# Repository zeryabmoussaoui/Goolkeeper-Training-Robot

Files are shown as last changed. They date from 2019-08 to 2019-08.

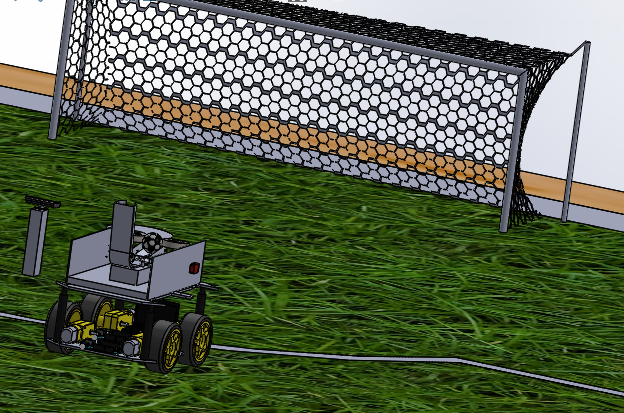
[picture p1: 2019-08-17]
hardware/mechanics/images/cad/Back_view.PNG

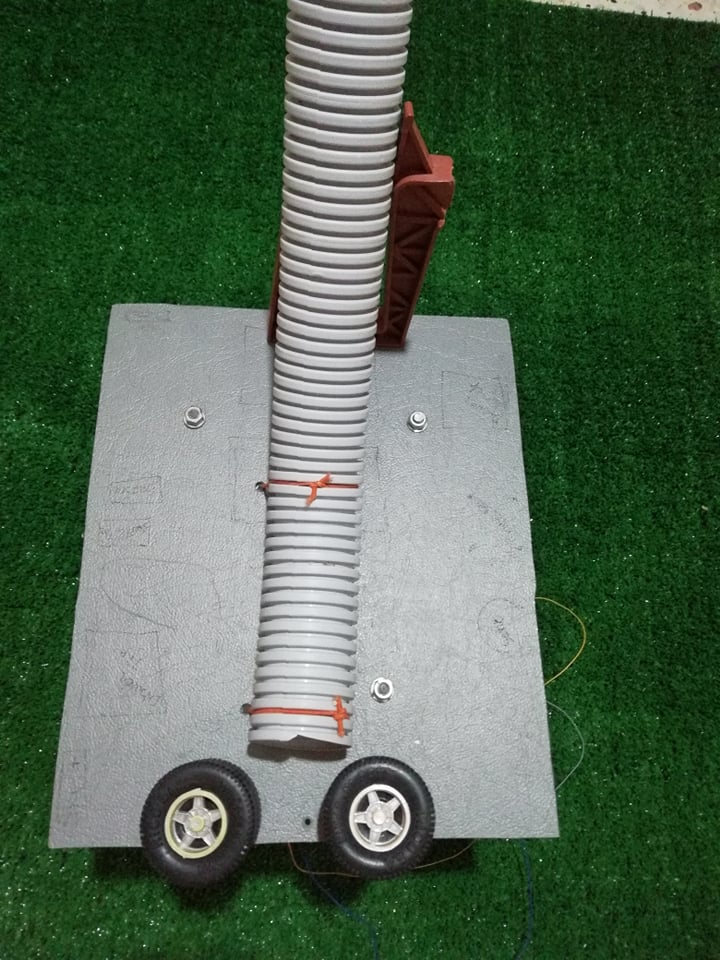
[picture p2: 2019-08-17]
hardware/mechanics/images/prototype/storage system/1.jpg

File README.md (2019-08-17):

# Goolkeeper-Training-Robot
In order to obtain the Engineering diploma in Automation field at the National Polytechnic School (Algeria) and in collaboration with the Central school of Electronics (France), I present to you my final thesis project, entitled **“Goalkeeper Training Robot”**.



## Summary
The project consists on the modeling and the realization of an autonomous robot that shoots
and evaluates the performances of a soccer goalkeeper based on his reactions.
Using a camera and a 3D human pose estimator, the system can detect and modelize the
goalkeeper’s physical gestures.
Finally, it proposes using artificial intelligence the suitable decision for the future exercises,
which maximizes the player’s performances.

## Folder structure
+ **README** 
  
+ **software/**
     - README
          - § Tool (Requirements , etc)
          - § Architecture (State-machine)
     - launch-train-goalkeeper.py 
     - launch-simulation.sh  
     - utils/ 
          - compute_pose.py
          - analyze_pose.py
          - send_navigation_mav.py
          - etc
+ **hardware/**
     - README
          - § List of components (existent and missing ones) 
     - mechanics/ 
          - cad_files/
          - images/
     - electronics/
          - cad-files/
          - images/
+ **articles/**
     - english
          - summary.docx 
          - summary.pdf
     - french
          - Mémoire_STIHI_Maha_ENP.pdf

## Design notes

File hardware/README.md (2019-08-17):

# Goolkeeper-Training-Robot

# Hardware

## List of available components 
| Component | Technical reference |
| --- | --- |
| DC motors | Pololu 12VDC, 350rpm 100:1 Gearmotor w/64 CPR Encoder | 
| DC motors | DC 12v motor | 
| Motor driver  | Cytron 10A 5-30V Dual Channel DC Motor Driver | 
| Autopilot | Pixhawk PX4 2.4.8 |
| Power supply  | DC 5v and 12v |
| Lipo battery  | Lipo 11.1 v 2200mah battery |
| Controling card  | Raspberry Pi 3 B+ |

## List of missing components 

| Component | Technical reference |
| --- | --- |
| Stepper motor | 2.8 V 1.68A 4.4kg-cm RepRap SOYO |
|  Motor driver | Single stepper motor driver 10-30V 4A |
| Power cable | Power cable for the Pixhawk PX4 2.4.8  | 

## Prototype 
Using the stated components and the mechanical structure design, we build the prototype of the system to represent most of the functionalities of the real system.

The steps of the construction are as follow :

**1. The base of the robot :**



**2. Shooting system :** 



**3. Storage system :** 



**4. Assembled robot :**



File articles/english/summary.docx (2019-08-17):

Design and Realization of a Mobile Robot to train Football Goalkeepers

Realized by: Maha Stihi

Abstract
The project consists on the modeling and the realization of an autonomous robot that shoots
and evaluates the performances of a soccer goalkeeper based on his reactions.
Using a camera and a 3D human pose estimator, the system can detect and modelize the
goalkeeper’s physical gestures.
Finally, it proposes using artificial intelligence the suitable decision for the future exercises,
which maximizes the player’s performances.
Key words: Soccer goalkeeper, Training, Robot, 3D human pose estimation, Artificial
intelligence.

I. Introduction

Robotics has many areas of application. Originally, the robots been established in industries (as early as 1961) to perform repetitive tasks with a constant precision. Now, after the development of technology and especially after the introduction of artificial intelligence, we find robots implanted in almost all fields and used for all purposes, even in an environment close to humans. The artificial intelligence algorithms and robots are known to be introduced to automate tasks and replace human work. For example, "LawGeex" uses the latest technologies in intelligence, machine learning, analysis text and natural language processing to review and understand documents legal [1]. This smart system can replace hundreds of legal advisers who are often overworked to review daily contracts, which was very expensive in time, money and human resources. In robotics and more specifically in sports field, athletes are also among the recipients of technological assistance. We can cite:

- Mobile robots developed by the "Japanese Volleyball Association" with the help of researchers from Tsukuba University to help the team's attackers National Women's Training [2] (Figure 1.a);

- The tennis ball shooter robot that gives precise and intensive training to players [3] (Figure 1.b);

- And also the mobile robot "MVP" that simulates the veneer of football players American [4] (Figure 1.c).

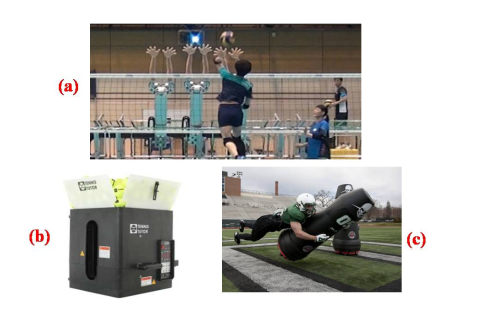
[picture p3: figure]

Figure 1 - Examples of sports robots

II. Problematic

In the field of sport, some techniques need a lot of training to master them. Even in the best teams in the world, the number of coaches is very limited, especially in football, for 4 goalkeepers only one coach is available. Therefore, players from different positions will help each other to ensure their training. What makes some players spend part of their workouts helping goalkeepers practicing.

Decision making has always been a difficult task; choose which player to introduce in a match is made by coaches based on several criteria like the physical and tactical performances of the player in the training. This decision is related to the skills and experiences of coaches, so it can be biased.

Injuries are the biggest enemies of athletes. Once the injury is treated medially, the player goes through special programs to return to his former performance. The follow-up of the players after a stoppage of play is a very important part; given that it determines the time it takes to get back to competition, so it can affect the whole team if he is an important player. The choices of the type and intensity of exercises are usually set by both medical and technical parties. By consequence, having a compromise between the medical team that wants to ensure that the player can play in security and the technical team that wants the player to return to the pitch as soon as possible is very difficult to ensure, so a neutral third opinion is highly recommended.

With this project, we want to contribute to a part of the sport field, which is the training of football goalkeepers to minimize the problems illustrated above.

We propose a mobile robot, to help the goalkeeper’s coach during the trainings and also to test the players’ performances with the help of the analysis of the goalkeeper's gestures based on well-studied exercises. Subsequently, the robot provides detailed technical reports to help the coach take the right decisions. It will also have an artificial intelligence that will help to propose the future exercises to work on to keep track of injuries and maximize players’ performances.

III. Specifications

In order to achieve our strategy, the robot must be able to:

- Move on a flat surface to position the coordinates (x, y) on the pitch;

- Turn it in a flexible way to orient the part of the shot at an angle θ with a good precision;

- Locate on the ground using odometers;

- Store the balls in the robot using the available height;

- Shoot the balls with a speed and a predefined trajectory;

- Estimate the pose of the goalkeeper;

- Analyze and study the goalkeeper's reaction to the shot.

IV. System Architecture

The modeling of the system allows us to establish a work plan of the project, by identifying the essential parts of the project and the relationships between them. This modeling allows us to have the architecture overall system.

The architecture of mobile robots consists of four essential parts:

• Mechanical structure and motorization;

• Location system;

• Security organs;

• Information processing system and task management.

This architecture is usually presented as a block diagram, each block represents a feature of the system, and the blocks are then linked together based on the logic of system operation.

Our project is more complex than a simple mobile robot because we have a ball shooting functionality as well as another external data processing feature of the goalkeeper. So, more blocks are presented in the architecture of our system.

Security organs are not taken into account in our work. Only basic security components are set up in our system.

To represent the system parts and its logic process, we use the Moore state diagram as followed:

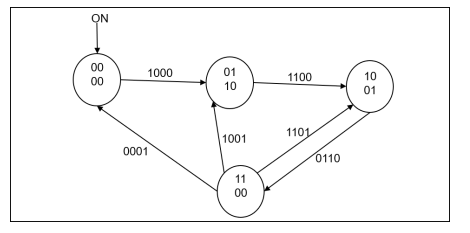
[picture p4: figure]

Outputs:

Motors moving & motors shooting

Position arrived

Shoot

Analysis

done

Exercise

State :

00 : initialization

01 : Move

10 : Shoot

11 : Analysis

Transition :

x | x | x | X

Fig 2– Moore diagram (state diagram)

In order to program this state machine in the future, we prefer to represent the state machine as known for the programmers:

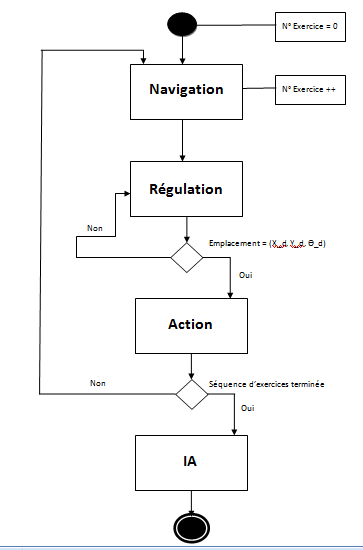
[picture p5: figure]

Fig 3 – State machine

V. Mechanical Conception

The mechanical design was done by SolidWorks, version 2016.

V.1. Mobile Robot Base

The top of the robot is dedicated to the shooting so, it’s bulky and heavy therefore, the upper surface must be spacious and solid. At the same time, robot must stay in balance to ensure a good trip on the pitch. So, we opted for a four-wheeled mobile base model "Rover" (Figure 4).

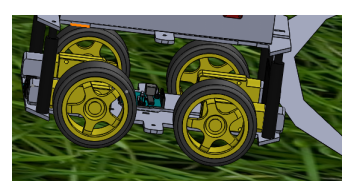
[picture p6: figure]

Figure 4 – Rover

V.2. Ball Shooting System

In order to ensure a variety of training exercises by our robot, it is necessary that the shooting system has the ability to generate different types of trajectories for the ball.

For this, this part of the robot must not be totally fixed. With two engines (Figure 5), a shooting angle of 30◦maximum can be achieved to aim at any point on the height of the goals.

On the other hand, the shooting is done using two motorized wheels with separate speeds, which makes it possible to vary the exit trajectory while varying the speeds of the two motors separately (Figure 5).

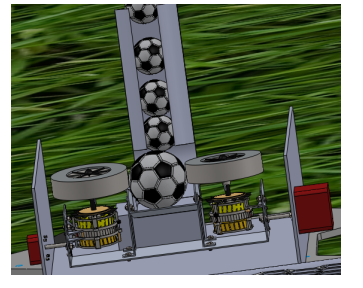
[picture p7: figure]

Figure 5 – Upper part of shooting balls

V.3. Storage System

To achieve several shots fast, automated, and also to avoid the human being assistance, a balloon storage system is necessary. We designed a cylindrical device with a diameter of 28 cm, which allows stacking footballs (diameter 22 cm) vertically.

Only one ball must pass at a time and on demand to the shooting part, for this a motorized controllable blocking system is implemented (Figure 6).

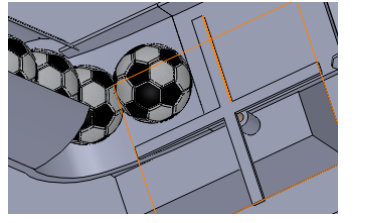
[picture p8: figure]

Figure 6 – Ball blocking system

V.4. Robot Assembly

The previous three parts are assembled to form our robot balls shooter (Figures 7 and 8).

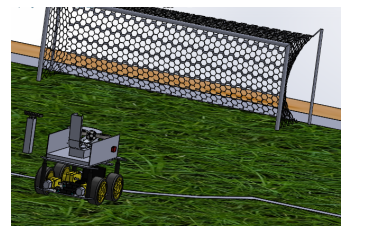
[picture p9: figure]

Figure 7 – Back view of the robot.

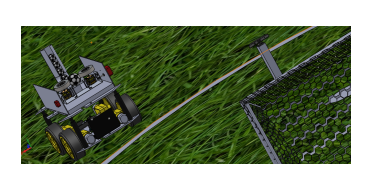
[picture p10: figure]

Figure 8 – Front view of the robot.

VI. Rover Simulation

Before jumping into the realization of the real robot and test the navigation system, it’s preferable to test the programs and functionalities with a simulation.

Ardupilot is an open source (https://en.wikipedia.org/wiki/Open-source_software), unmanned vehicle (https://en.wikipedia.org/wiki/Uncrewed_vehicle) Autopilot navigation software capable of controlling autonomously different types of vehicles:

- Multirotor (https://en.wikipedia.org/wiki/Multirotor) drones
- Fixed-wing and VTOL (https://en.wikipedia.org/wiki/VTOL) aircraft (https://en.wikipedia.org/wiki/Model_aircraft)
- Helicopters (https://en.wikipedia.org/wiki/Radio-controlled_helicopter)
- Ground rovers (https://en.wikipedia.org/wiki/Radio-controlled_car)
- Boats
- Submarines (https://en.wikipedia.org/wiki/Radio-controlled_submarine)
- Antenna trackers

Ardupilot proposes also simulation functionality, using many knows simulators.

Rover is an advanced open source (http://ardupilot.org/dev/docs/license-gplv3.html) autopilot for guiding ground vehicles and boats. It can run fully autonomous missions that are defined using mission planning software or pre-recorded by the driver during a manual run.

Rover runs on the Pixhawk (http://ardupilot.org/rover/docs/common-pixhawk-overview.html) and a number of other supported autopilot boards (http://ardupilot.org/rover/docs/common-autopilots.html).

For our project we used:

- Simulator : Software In The Loop (SITL)
- Operating system: Linux
- Vehicle: Rover2
- Parameters: wind, speed, environment...

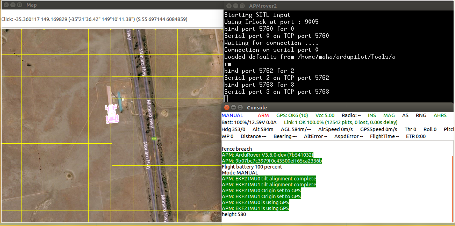
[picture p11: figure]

Fig 9 – Realized simulation using Ardupilot

VII. Prototype

Once the robot modelization and the simulation done, we pass to the prototyping.

The prototype does not contain all the functionalities of the real robot for complexity reasons.

The steps of the realization are represented below:

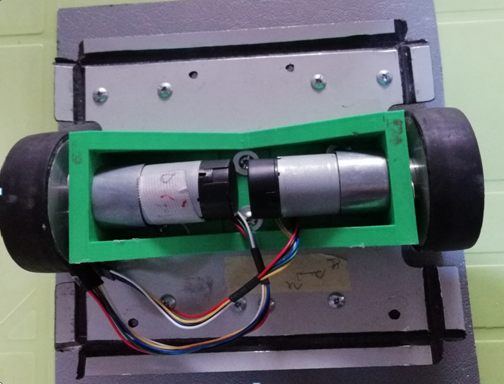
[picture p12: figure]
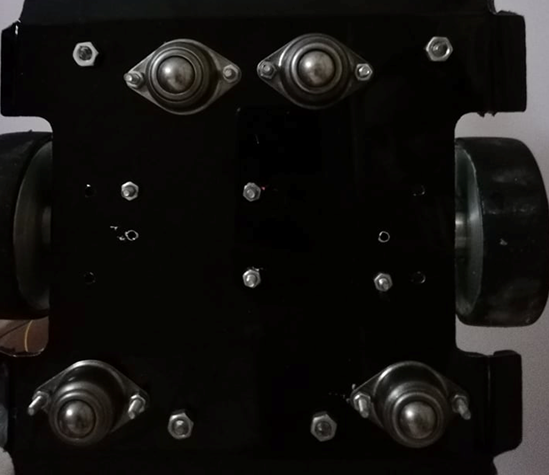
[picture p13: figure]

Fig 10 – Mobile base with 2 motorized DC motors and 4 free wheels

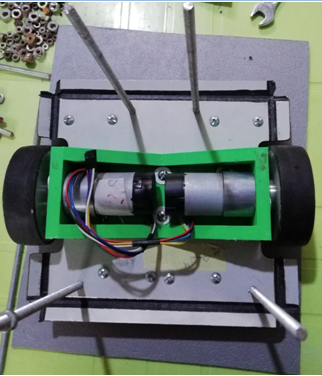
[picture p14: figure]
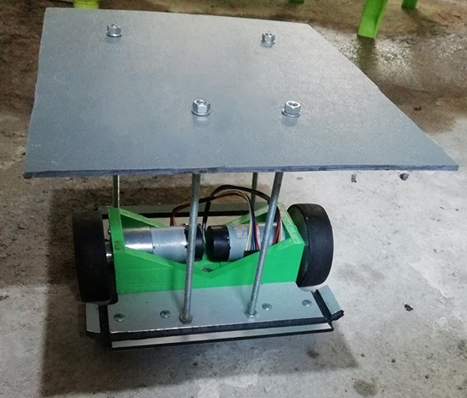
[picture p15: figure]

Fig 11 – Second level for the shooting dispositive

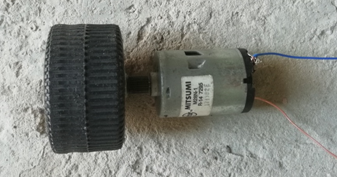
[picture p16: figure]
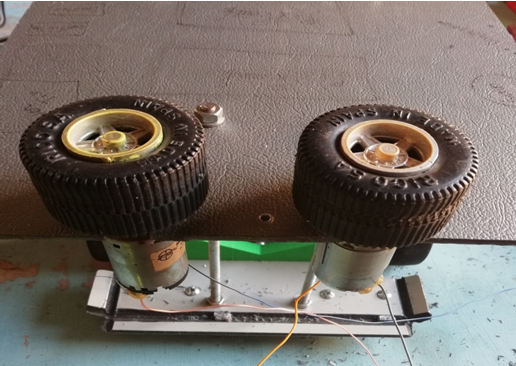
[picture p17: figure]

Fig 12 – Shooting system

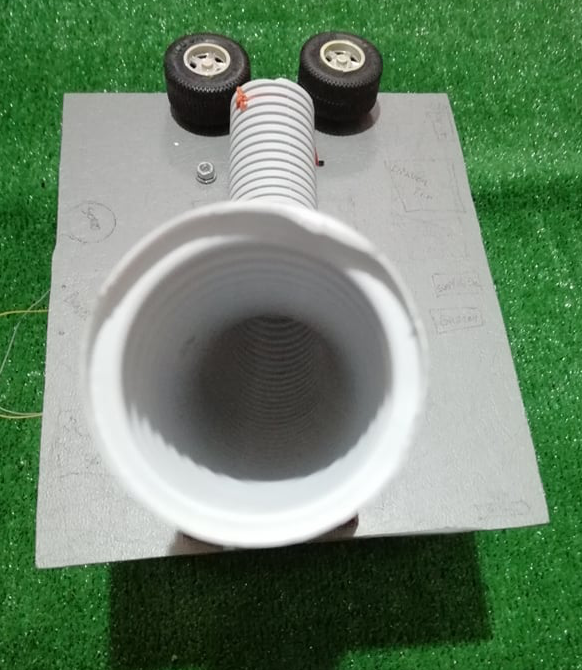
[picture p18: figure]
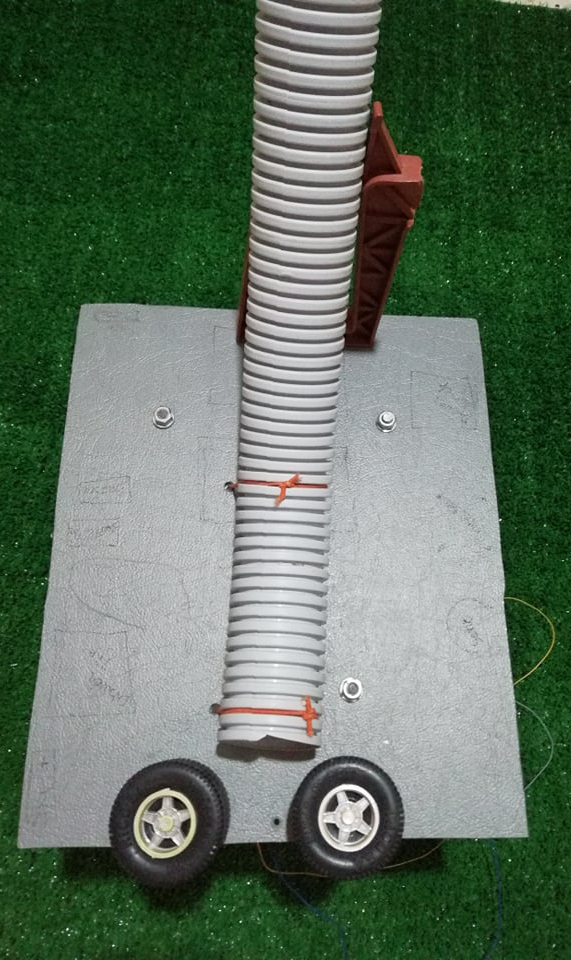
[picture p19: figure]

Fig 13 - Storage system

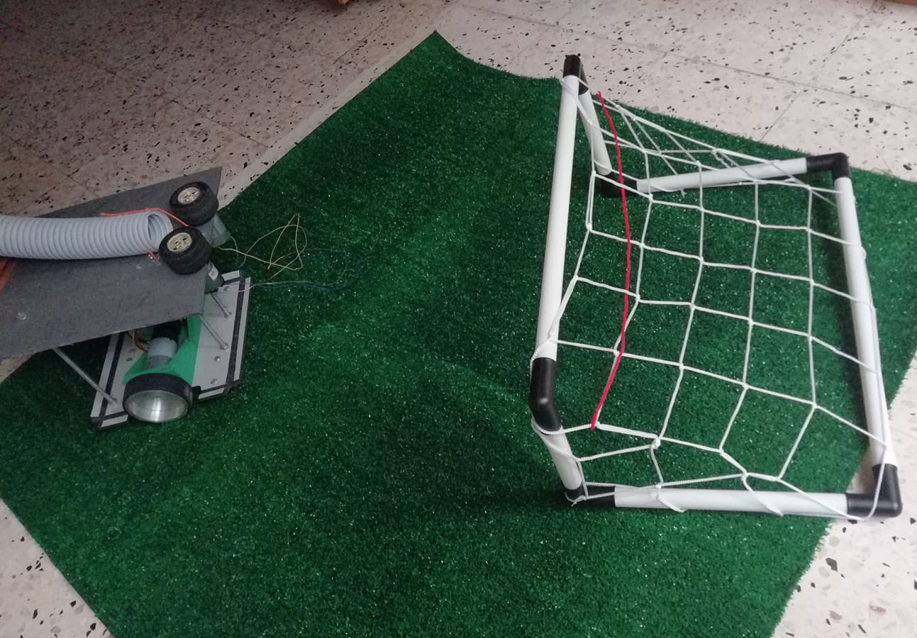
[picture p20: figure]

Fig 14 – Assembled robot

VIII. Human Pose Estimation

A video is collected after the shooting to evaluate the goalkeeper’s reactions. For this, we need to apply a human pose estimator on it to have exploitable (numerical) information. This numerical information will be used in the data analysis part.

Although many pose detection/estimation systems exist and in addition are in open source, many of them require specialized hardware and / or cameras, as well as many system configurations. The most flexible and accessible pose estimator we have chosen is "PoseNet" which functions on "TensorFlow.js". For our prototype, we use a RGB camera.

PoseNet (https://github.com/tensorflow/tfjs-models/tree/master/posenet) can be used to estimate either a single pose or multiple poses, meaning there is a version of the algorithm that can detect only one person in an image/video and one version that can detect multiple persons in an image/video.

At a high level pose estimation happens in two phases:

1. An input RGB image is fed through a convolutional neural network.
2. Either a single-pose or multi-pose decoding algorithm is used to decode poses, pose confidence scores, keypoint positions, and keypoint confidence scores from the model outputs.

Pose — at the highest level, PoseNet will return a pose object that contains a list of keypoints and an instance-level confidence score for each detected person.

- Pose confidence score — this determines the overall confidence in the estimation of a pose. It ranges between 0.0 and 1.0. It can be used to hide poses that are not deemed strong enough.
- Keypoint — a part of a person’s pose that is estimated, such as the nose, right ear, left knee, right foot, etc. It contains both a position and a keypoint confidence score. PoseNet currently detects 17 keypoints illustrated in the following Figure :

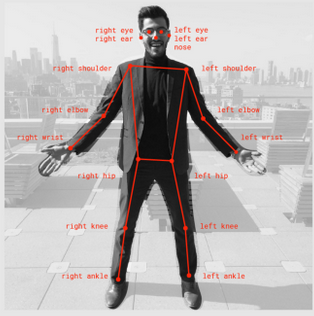
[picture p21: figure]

Fig 15 – 17 keypoints returned by PoseNet

- Keypoint Confidence Score — this determines the confidence that an estimated keypoint position is accurate. It ranges between 0.0 and 1.0. It can be used to hide keypoints that are not deemed strong enough.
- Keypoint Position — 2D x and y coordinates in the original input image where a keypoint has been detected.

The html program provided by PoseNet was used to test our project situations (Figure 16) [5].

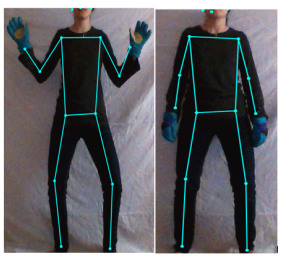
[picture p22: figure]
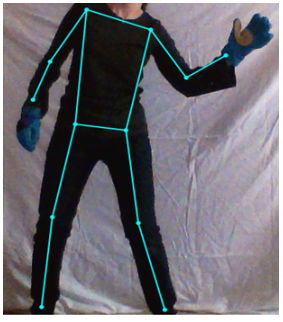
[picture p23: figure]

Fig 16 – Real time human pose estimation using PoseNet

The pose estimator reacted well to the movements, but the precision and the speed need to be improved to apply it for real time goalkeeper’s reactions analysis.

IX. Data Analysis

The acquired data from the pose estimation of the goalkeeper will be used to analyze his reactions and determine either he made the good gestures or not.

After many exercises the strength and weakness of the goalkeeper can be determined.

For the technique of analysis, two methods were studied and compared:

  1. Machine learning
  2. Fuzzy logic

The comparison between the two methods is as follow:

1. Machine learning

• Chosen technique: supervised learning "supervised learning"

• Estimated data collection time: 40h

• Estimated training time: 10h

• Estimated time of tests and implementation: 20h

• Method of data collection: manual (video games)

2. Fuzzy logic

• Chosen technique: fuzzy logic type 1

• Estimated data collection time: 8h

• Estimated time of system understanding: 12h

• Estimated time of tests and implementation: 10h

• Method of data collection: manual (with an expert)

X. Conclusion and perspectives

We managed to model the system’s parts: Mechanics, Automation and Computer Science as well as the construction of a small prototype of the robot balls shooter.

Regarding the analysis part, we worked on a human pose estimator that provides the data needed to interpret the goalkeeper's reactions.

Note that with the limited time available and taking into account the diversity and complexity of each part of the project, we have achieved a proof of concept and not a finished product. In order to present a product with high precision, finished and robust we propose that each part of the system be treated separately so, the performances of the different constituents of the training system will be strengthened.

Improving the accuracy of the human pose estimation requires the use of a more powerful camera, for example the kinect. The algorithm used for estimation can be improved too using one of the state-of-the-art methods.

The implementation of artificial intelligence, whose role is to interpret the reactions
the goalkeeper and propose new exercises, can be done in two ways:

Machine Learning or fuzzy logic. It is better to dedicate a project dedicated to this part
data analysis in order to have usable results.

Bibliography

[1] LAWGEEX . About us, [Online]. https://www.lawgeex.com/aboutus. [Page consulted: 01/20/2019].

[2] NUMERAMA. L’équipe Féminine Japonaise de Volley-ball s’Entraine avec un Robot
[Online]. https://www.numerama.com/tech/249453-lequipe-feminine-japonaise.

[3] DOCPLAYER. Lancer Balles de Tennis Tutor 4 Plus Player [Online]. https://docplayer.fr/29115688-Lance-balles-tennis-tutor-4-plus-player.html . [Page consulted : 01/22/2019].

[4] LE TEMPS. Un Robot Sécurise le Placage d’un Terrains de Football Américan, [Online]. https://www.letemps.ch/sciences/terrains-football-americain-un-robotsecurise placages. [Page consulted: 01/22/2019].

[5] MEDIUM.Real_Time-Human-Pose-Estimation-in-the-Browser-with-TensorFlow.js.[Online] https://medium.com/tensorflow/real-time-human-pose-estimation-in-the-browser-with-tensorflow-js-7dd0bc881cd5. [Page consulted: 06/15/2019].

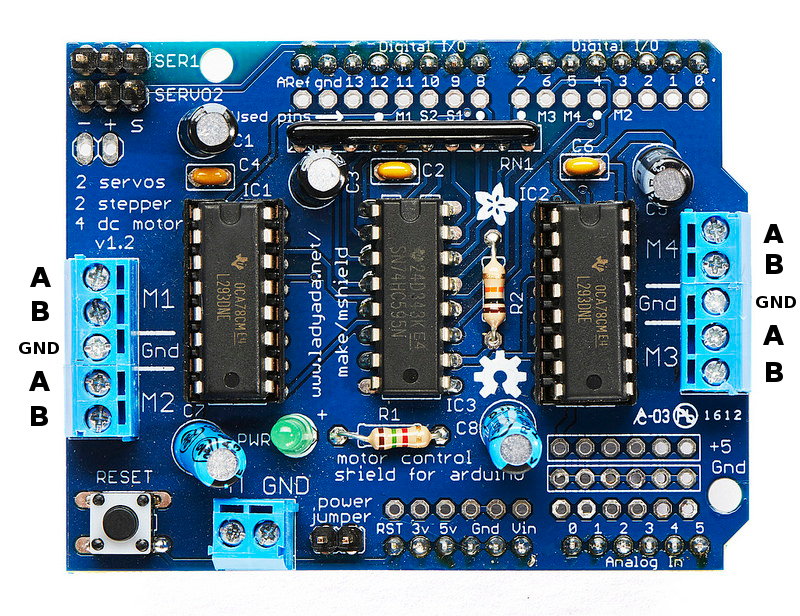
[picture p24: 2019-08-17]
hardware/electronics/images/Motor driver shield Arduino (Shooting system).jpg

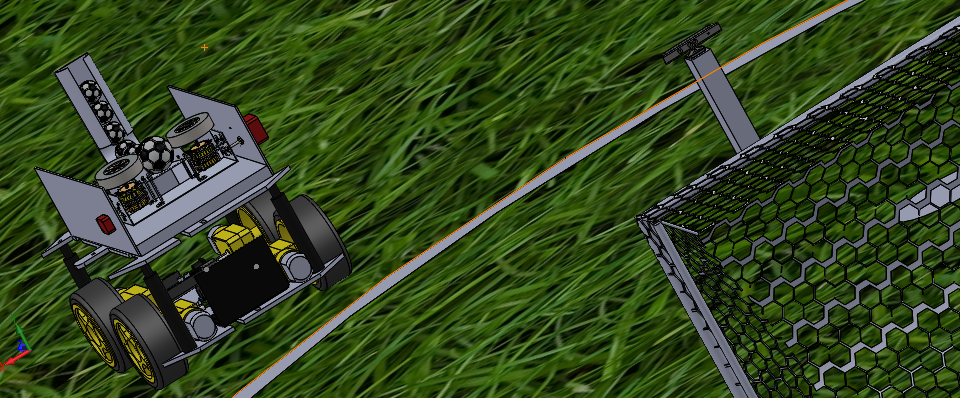
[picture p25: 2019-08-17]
hardware/mechanics/images/cad/Front_view.PNG

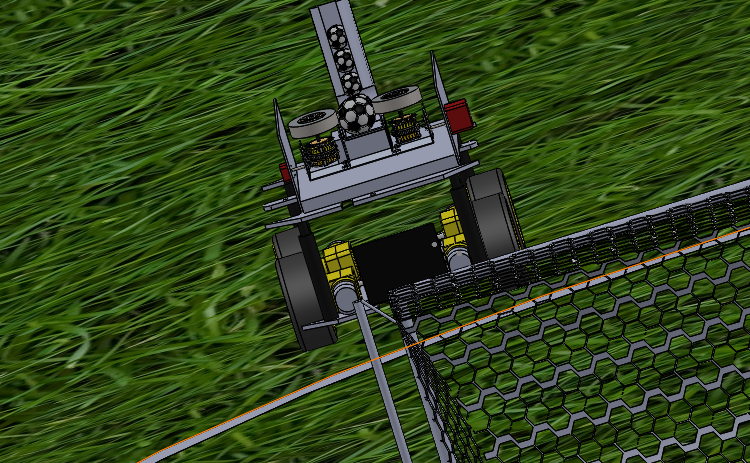
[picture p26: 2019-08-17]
hardware/mechanics/images/cad/Robot.PNG

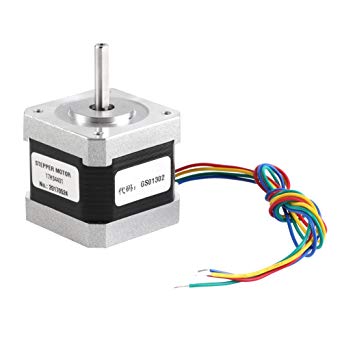
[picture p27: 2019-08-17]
hardware/electronics/images/Stepper 17HS4401 Nema.jpg

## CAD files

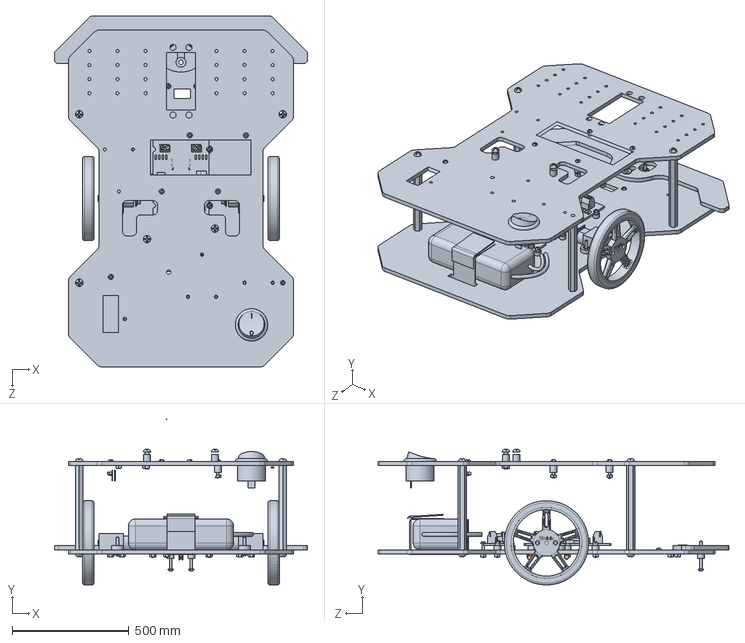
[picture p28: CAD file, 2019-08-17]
hardware/mechanics/cad_files/parts/base/Base.SLDASM
1083.0 x 708.8 x 1500.0 mm
Global
STEINCO CASTER_try_02 x 2

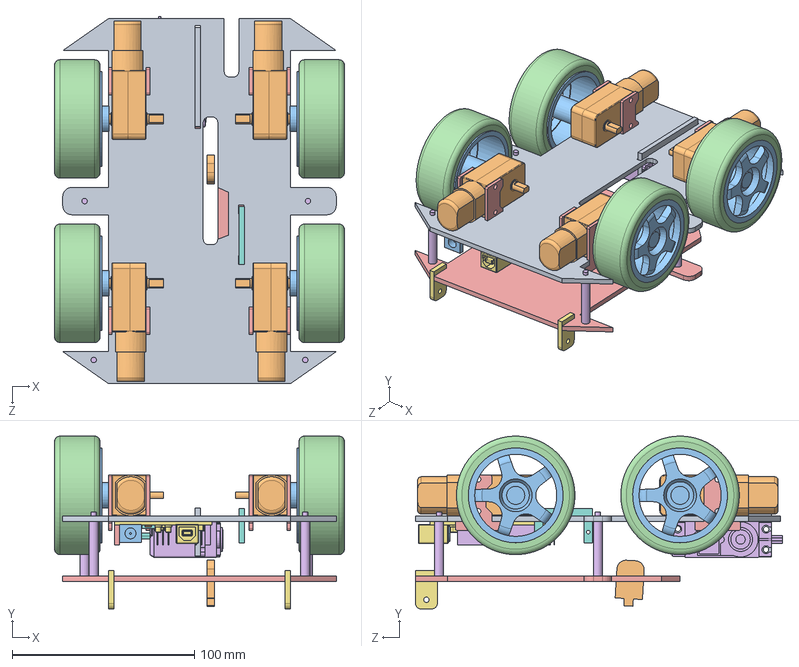
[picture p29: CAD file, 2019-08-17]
hardware/mechanics/cad_files/parts/rover/rover.SLDASM
159.0 x 94.8 x 201.2 mm
Base
Motor Kuning x 4
rim x 4
tire x 4
Braket Gearbox Kuning 2 x 8
TowerPro-MG995
board
ZZ
pin1
pin2 x 28
Base Top
4cm x 4
Poros Bak Sampah x 2
Braket Servo Kecil
Braket Servo Besar
Pen Poros Trash Box

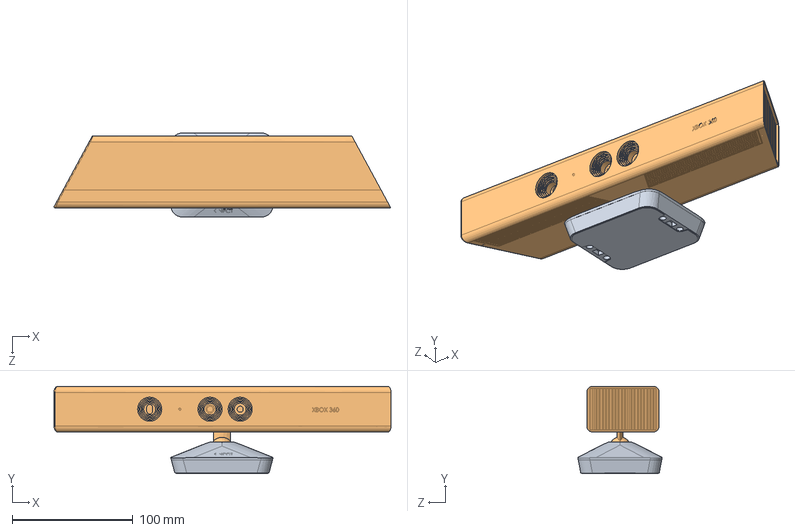
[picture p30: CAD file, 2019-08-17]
hardware/mechanics/cad_files/parts/kinect/kinect-1.snapshot.2/final kinect.SLDASM
279.3 x 72.5 x 70.0 mm
lower part
kinect upper part

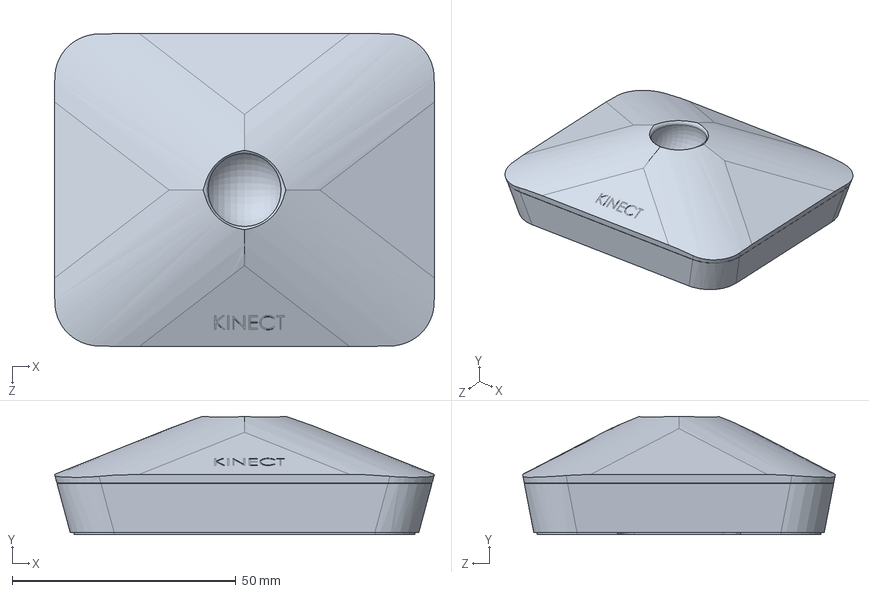
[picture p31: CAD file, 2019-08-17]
hardware/mechanics/cad_files/parts/kinect/kinect-1.snapshot.2/lower part.SLDPRT
85.0 x 26.5 x 70.0 mm

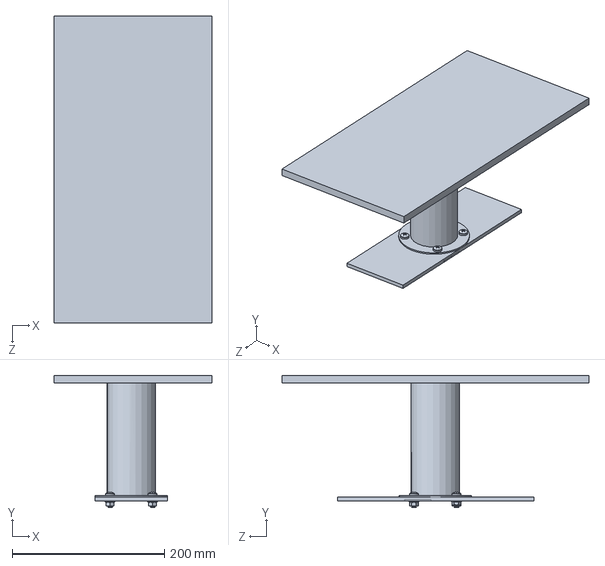
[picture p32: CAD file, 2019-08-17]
hardware/mechanics/cad_files/parts/pitching/football-throwing-machine/Motor_base.SLDPRT
207.3 x 174.0 x 403.2 mm

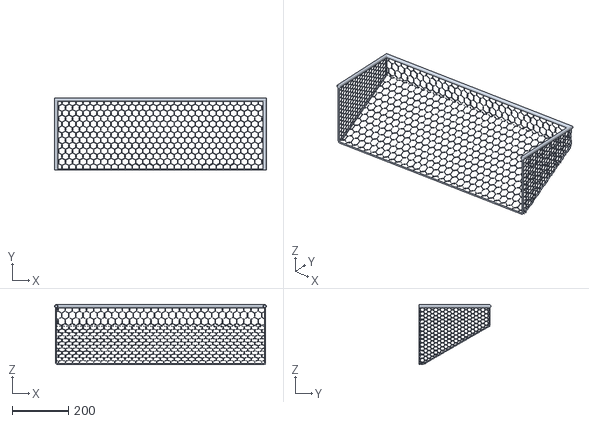
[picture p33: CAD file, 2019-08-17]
hardware/mechanics/cad_files/parts/soccer-goal/FootballGoal.stl
756.0 x 256.0 x 214.0

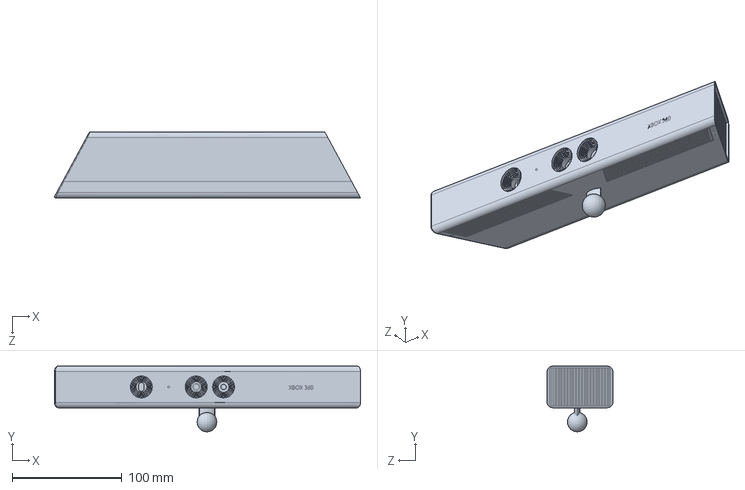
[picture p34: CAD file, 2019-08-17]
hardware/mechanics/cad_files/parts/kinect/kinect-1.snapshot.2/kinect upper part.SLDPRT
279.3 x 60.0 x 60.0 mm

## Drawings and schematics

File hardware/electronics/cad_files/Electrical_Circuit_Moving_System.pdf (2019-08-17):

## Motor Left Motor Right

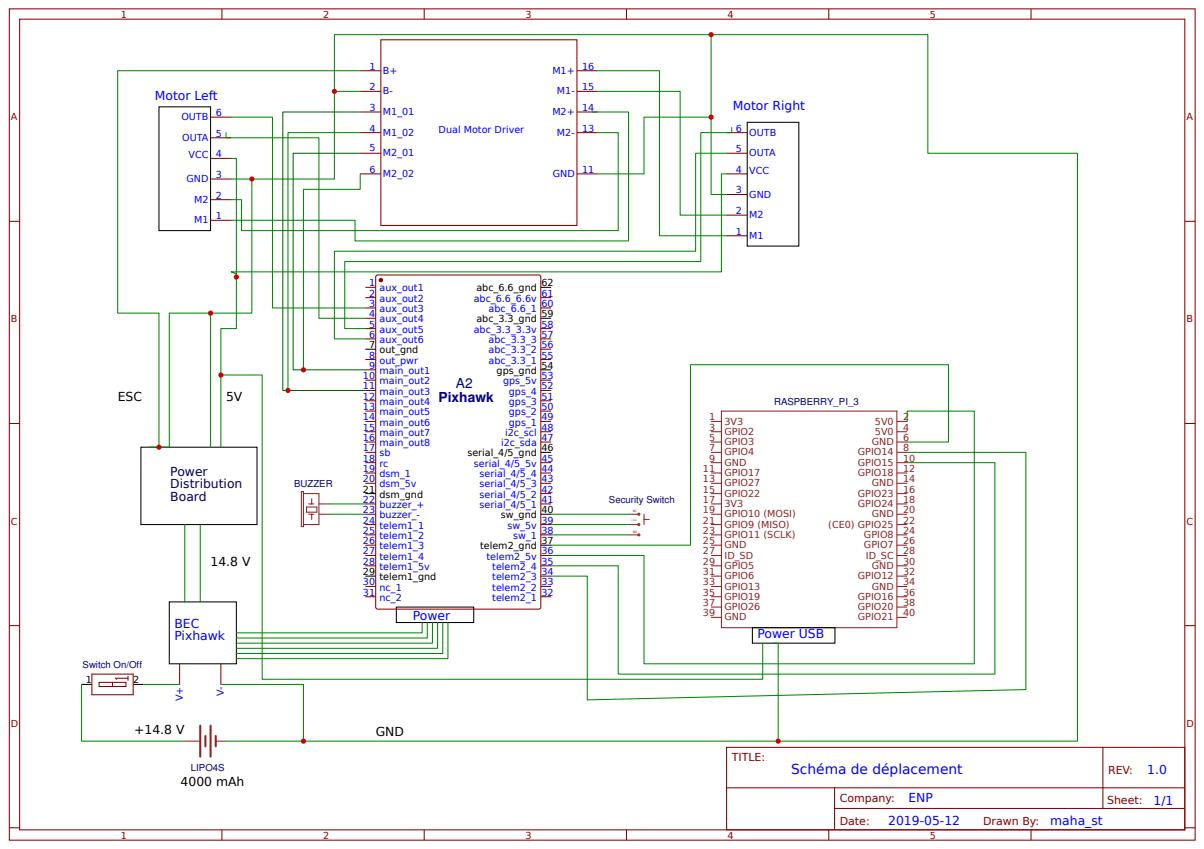
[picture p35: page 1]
TITLE:; Schéma de déplacement; REV: 1.0; Date:; Sheet: 1/1; Drawn By: maha_st; Company: ENP; Pixhawk; aux_out1 1 aux_out2 2 aux_out3 3 aux_out4 4 aux_out5 5 aux_out6 6 out_gnd 7 out_pwr 8 main_out1 9 main_out2 10 main_out3 11 main_out4 12 main_out5 13 main_out6 14 main_out7 15 main_out8 16 sb 17 rc 18 dsm_1 19 dsm_5v 20 dsm_gnd 21 buzzer_+ 22 buzzer_- 23 telem1_1 24 telem1_2 25 telem1_3 26 telem1_4 27 telem1_5v 28 telem1_gnd 29 nc_1 30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

Dual Motor Driver

Security Switch NC

Switch On/Off

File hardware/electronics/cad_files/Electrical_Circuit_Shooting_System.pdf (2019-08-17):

## Motor Left

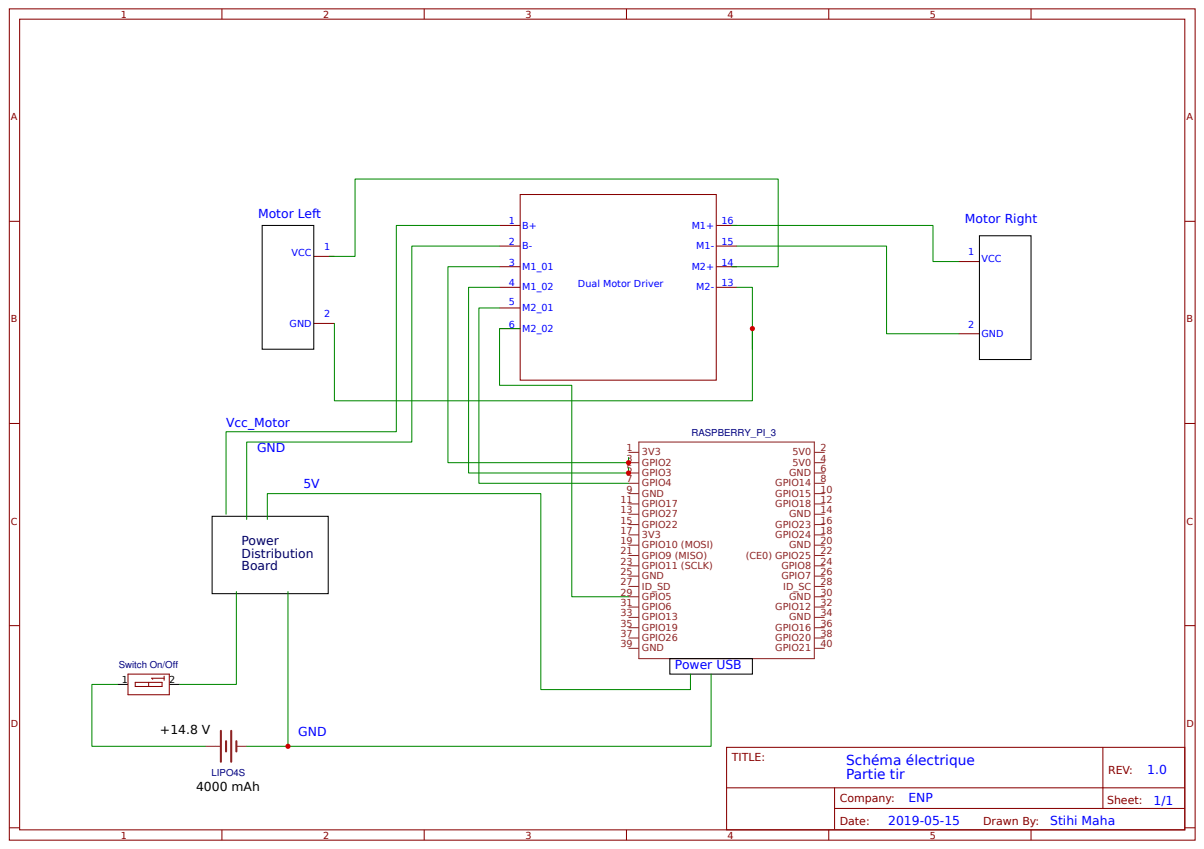
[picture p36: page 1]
TITLE:; Schéma électrique; Partie tir; REV: 1.0; Date:; Sheet: 1/1; Company: ENP; GND; VCC 1; Motor Right; Power Distribution Board; LIPO4S; 4000 mAh; RASPBERRY_PI_3; GPIO2 3; GPIO3 5; GPIO4 7; GPIO14; GND 9; GPIO15; GPIO17 11; GPIO18; GPIO27 13; GPIO22 15; GPIO23; GPIO24; GPIO10 (MOSI) 19; GPIO9 (MISO) 21; (CE0) GPIO25; GPIO11 (SCLK) 23; GPIO8; GND 25; GPIO7; GPIO5 29; GPIO6 31; GPIO12; GPIO13 33; GPIO19 35; GPIO16; GPIO26 37; GPIO20; GND 39; GPIO21; Power USB; Vcc_Motor

Dual Motor Driver

Switch On/Off

Drawn By: Stihi Maha

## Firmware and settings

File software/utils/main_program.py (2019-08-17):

# In the main program, we program the state machine 
# import all the sub programs that represent the different states and extra features like the LEDs indicators
# import ....

"""##===============================================================================================================##"""
## Finite State Machine :

class FSM(object):
    def __init__(self, character):
        self.char=character
        self.states = {}
        self.transitions = {}         
        self.curState = None
        self.trans = None

    def AddState(self, stateName, state):
        self.states[stateName] = state

    def AddTransition(self, transName, transition):
        self.transitions[transName] = transition
    
    def SetState(self, stateName):
        self.curState = self.states[stateName]
    
    def ToTransition(self, toTrans):
        self.trans = self.transitions[toTrans]

    def Execute(self):
        if(self.trans):
              self.curState.Exit()
              self.trans.Execute()
              self.SetState(self.trans.toState) #toState ? 
              self.curState.Enter()
              self.trans = None
        self.curState.Execute()

"""##===============================================================================================================##"""
## IMPLEMENTATION 

Char= type("Char",(object,),{})

class Robot(Char):
    def __init__(self):
        self.FSM=FSM(self)

        ##STATES
        self.FSM.AddState("Initialisation", Initialisation(self.FSM))
        self.FSM.AddState("Move", Move(self.FSM))
        self.FSM.AddState("Analize", Analize(self.FSM))
        self.FSM.AddState("Shoot", Shoot(self.FSM))        	

        ##TRANSITIONS
        self.FSM.AddTransition("toInitialisation", Transition("Initialisation"))
        self.FSM.AddTransition("toMove", Transition("Move"))
        self.FSM.AddTransition("toShoot", Transition("Shoot"))
        self.FSM.AddTransition("toAnalize", Transition("Analize"))

        self.FSM.SetState("Initialisation")

    def Execute(self):
        self.FSM.Execute()

    def SetState(self, stateName):
        self.FSM.SetState(stateName)
    
    def ToTransition(self, toTrans):
        self.FSM.ToTransition(toTrans)

    def Update(self):
        global inputs
        # Updates
        inputs = "1000"
"""##===============================================================================================================##"""
#Main Program
if __name__ == '__main__':
    r = Robot()
    while True:
         r.Execute()
         r.Update()
         r.Execute()

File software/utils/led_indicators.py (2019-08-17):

# LED indicators
# We installed 4 LEDs on the prototype :
# 1. Blue  : ball releasing demand
# 2. Red   : system off
# 3. White : shooting angle required
# 4. Green : new exercise
# The blue one has its own program that we import here "ball_releasing"


import RPi.GPIO as GPIO          
from time import sleep
from ball_releasing_system import init
from file import ball_release

Red=13
White=6
Green=26

def init ():
    GPIO.setmode(GPIO.BCM)
    GPIO.setup(Red,GPIO.HIGH)
    GPIO.setup(White,GPIO.OUT)
    GPIO.setup(Green,GPIO.OUT)

    GPIO.setup(Red,GPIO.LOW)
    GPIO.setup(White,GPIO.LOW)
    GPIO.setup(Green,GPIO.LOW)

def LEDs(exercise, angle):
    init()
    if exercice==1:
        GPIO.setup(Red,GPIO.LOW)
        print("System ON")
        GPIO.setup(Green,GPIO.HIGH)
        print("New exercise")
        
    else:
        GPIO.setup(Green,GPIO.LOW)
        print("No exercise")
        GPIO.setup(Red,GPIO.HIGH)
        print("System OFF")
    ball_release(exercice)

    if angle != 0:
        GPIO.setup(White,GPIO.HIGH)
    else:
        GPIO.setup(White,GPIO.LOW)
    print("Shooting angle : "+ angle)
        
